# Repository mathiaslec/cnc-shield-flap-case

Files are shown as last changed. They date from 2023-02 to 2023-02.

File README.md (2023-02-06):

# Read the documentation here : https://mathiaslec.github.io/cnc-shield-flap-case/
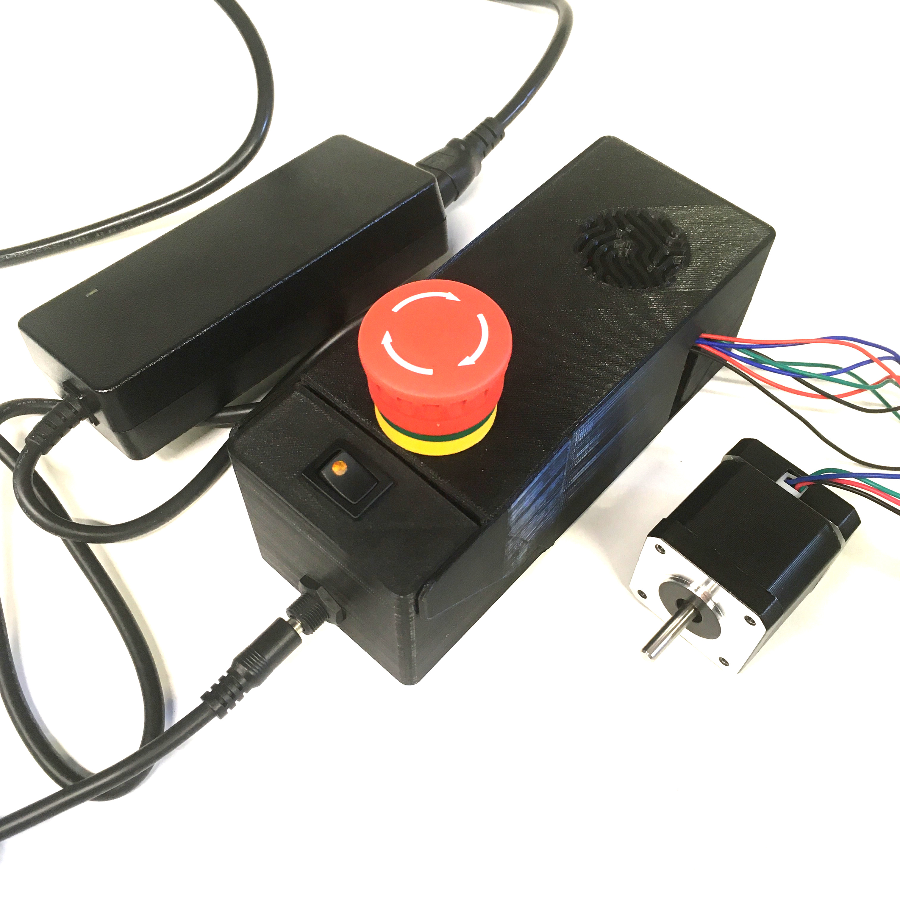
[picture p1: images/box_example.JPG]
  
# This project is documented with GitBuilding

## What is GitBuilding

GitBuilding is an OpenSource project for documenting hardware projects with minimal
effort, so you can stop writing and GitBuilding. GitBuilding is a python program that
works on Windows, Linux, and MacOS. More information on the GitBuilding project, or how
to install GitBuilding please see the [GitBuilding website](http://gitbuilding.io)

## How do I edit the documentation?

To edit the documentation you do not need to install anything, but you will need to
install something to build the final version of the documentation (such as a website).
The documentation files can be opened in a plain text editor such as Windows Notepad,
Notepad++, gedit, VS Code, etc. GitBuilding also comes with a browser-based editor that
displays has a live display of the final HTML documentation.

If you have ever used [markdown](https://www.markdownguide.org/basic-syntax/) you will
notice that the files you are editing are markdown files. GitBuilding uses an extended
markdown syntax (that we call BuildUp). This allows you to keep track of parts in the
documentation. More detail on the documentation is available on the
[GitBuilding website](https://gitbuilding.io/syntax/). There is also additional
[syntax for configuration](https://gitbuilding.io/syntax/buildconfsyntax), and for
[part libraries](https://gitbuilding.io/syntax/builduplibrary/).

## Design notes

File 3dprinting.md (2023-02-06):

# 3D printing

{{BOM}}

The CAD parts for the flap case were created using FreeCAD and are available on the [GitHub repository linked](freecad/cad/psu_xs_V5.FCStd).

The case is composed of three parts: the base, a small lid, and the main lid. The components are made with [PLA](parts.yaml#pla){qty:150g} material using a [FDM 3D printer](tools.yaml#3dprinter){qty:1, cat:tool}.

## Slicing {pagestep}
  
Download the stl files and upload them into your slice : 




We use Cura or Kiri:moto as slicer, with the following paremeters :  

* Layer height : 0.2 mm;
* Infill : 20 %;
* Supports everywhere;
* Wall thickness : 1.2 mm.

This is what the parts look like in the slicer :  
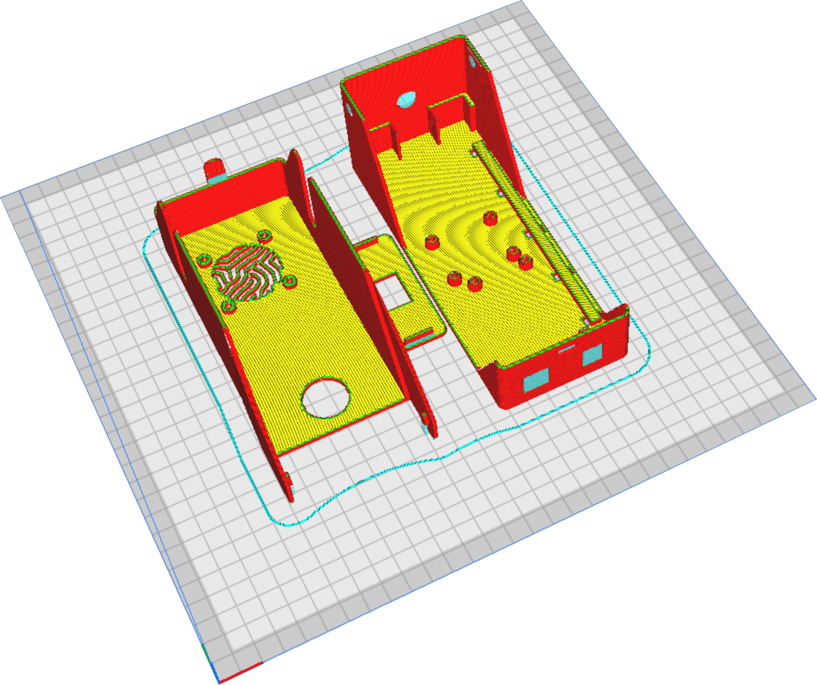
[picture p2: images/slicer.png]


## Post-printing {pagestep}
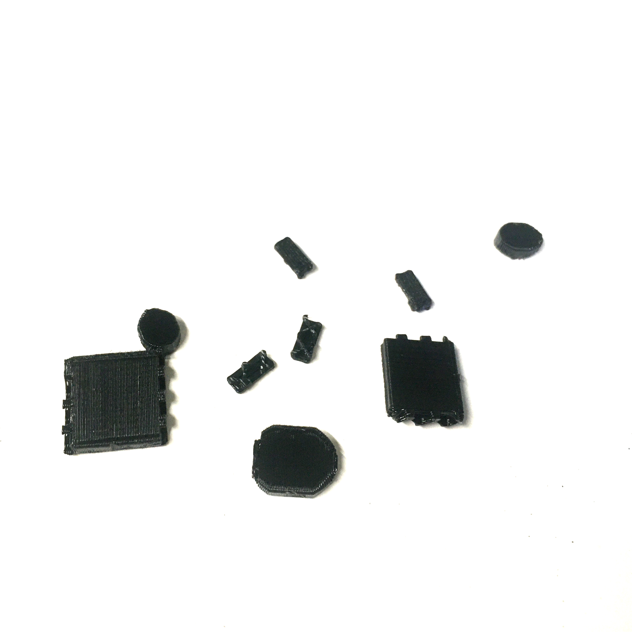
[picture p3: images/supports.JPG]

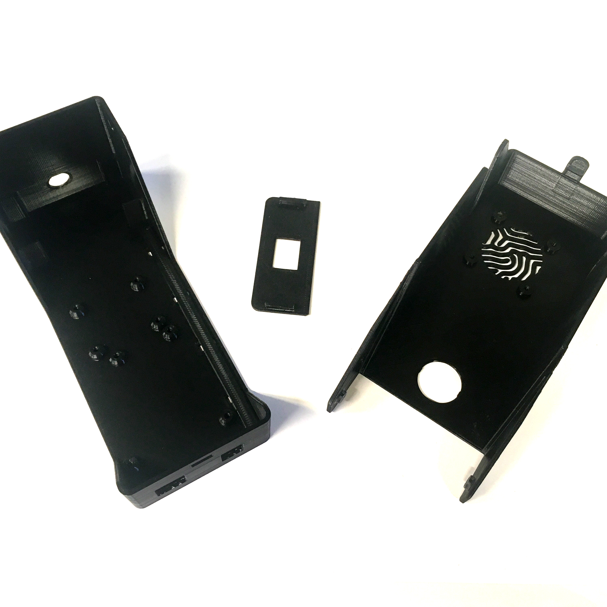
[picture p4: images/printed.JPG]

Once printed, carefully remove all supports.

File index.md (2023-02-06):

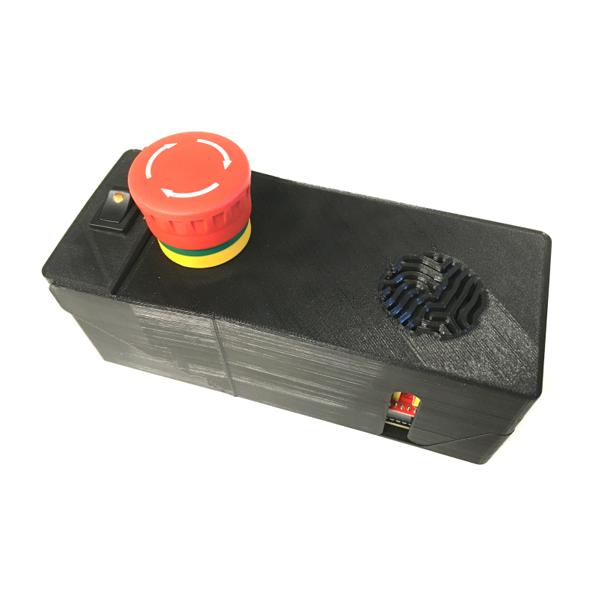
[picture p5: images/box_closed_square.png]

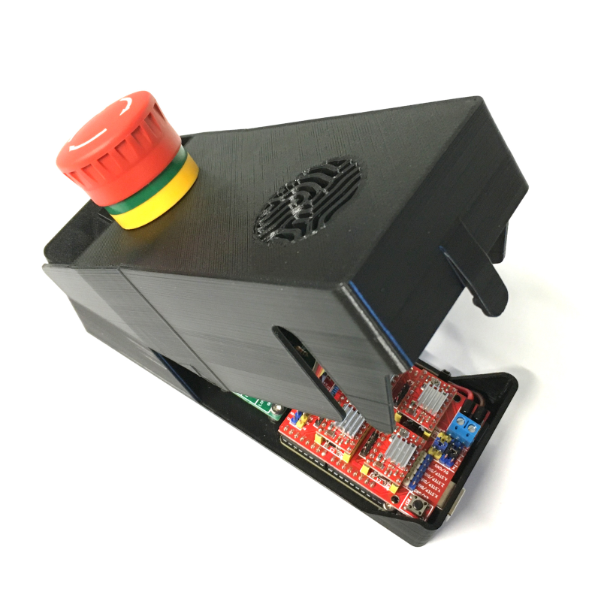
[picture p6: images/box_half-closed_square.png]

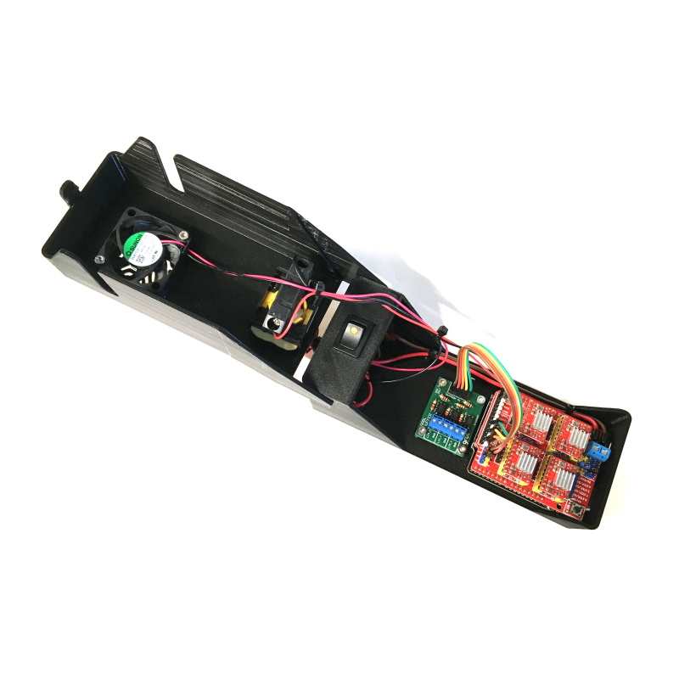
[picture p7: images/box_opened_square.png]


# CNC shield flap case

## Introduction

This is a tutorial on how to make a flap case for a CNC shield compatible with an Arduino Uno board.
Advantages of this flap case for a CNC shield include:

* A switch button with an LED to indicate the power status of the CNC shield and allow for easy ON/OFF control.
* A kill switch for emergency situations with the stepper motors.
* Easy access to the CNC shield for plugging and unplugging of stepper motors and limit switches, thanks to the flap design.

## Content

Here is the [bill of materials]{BOM} page.  
And here are the main steps to follow:

* [.](3dprinting.md){step}
* [.](assembling.md){step}
* [.](testing.md){step}
* [.](more_info.md){step}

## A few explanations about the design
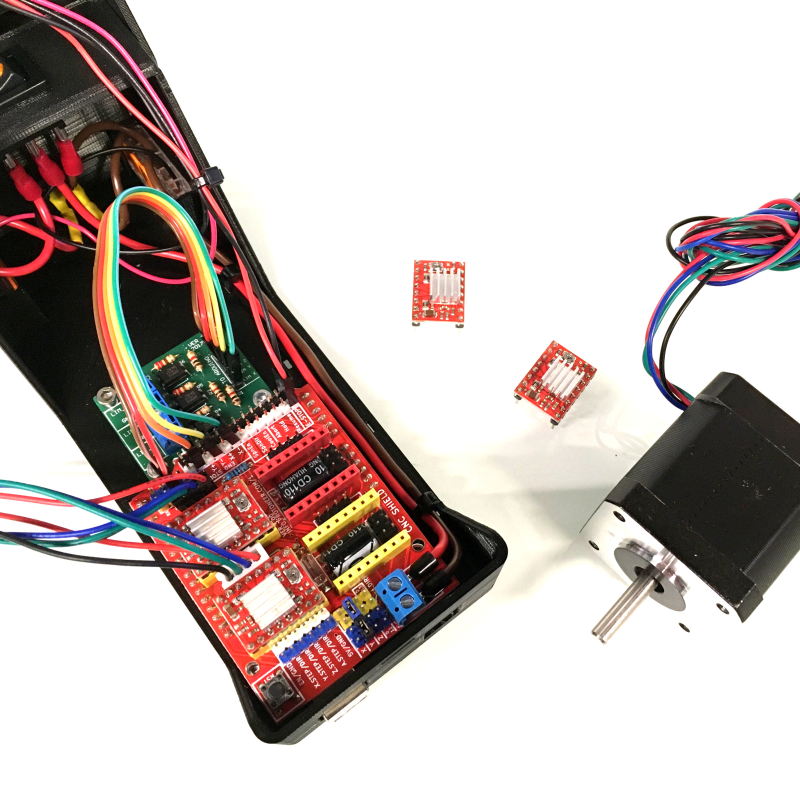
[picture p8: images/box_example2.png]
  
  
As shown in the images, the flap case is designed for easy plugging and unplugging of the stepper motors. The switch button with an LED helps to quickly and safely control the power status of the CNC shield.

Additionally, the flap case offers practicality and a touch of personal flair for those using CNC shields with multiple devices in various locations.

The fan grill on the flap case is a [Turing pattern](https://en.wikipedia.org/wiki/Turing_pattern), reference to the Turing Center for Living Systems, inspired by Alan Turing's work.

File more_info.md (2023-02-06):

# More information
## About the components
The power supply used is 12V 6.67A (80W), which should be enough for driving 4 stepper motors. All components are therefore chosen to carry at least 12V 6.67A (except for the fan which draws 95mA): wires, connectors, etc...

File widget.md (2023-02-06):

---
PartData:
    Specs:
        Type: Unknown
        Quality: Fantastic
    Suppliers:
        Widget Shop:
            PartNo: Widget1
            Link: https://dictionary.cambridge.org/dictionary/english/widget
---

# Widget

This is an example page for a part that needs more information than can be provided
in a part library. You can also add links and images into this page.



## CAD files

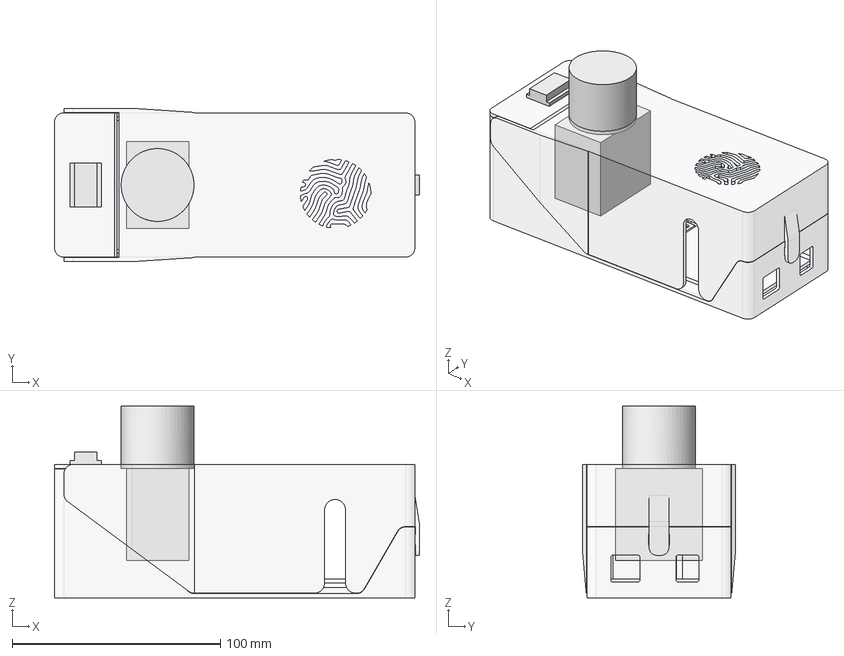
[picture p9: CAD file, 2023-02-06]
freecad/cad/psu_xs_V5.FCStd
175.3 x 73.7 x 92.0 mm
base
small_lid
lid
arduino_board
pcb
estop
switch

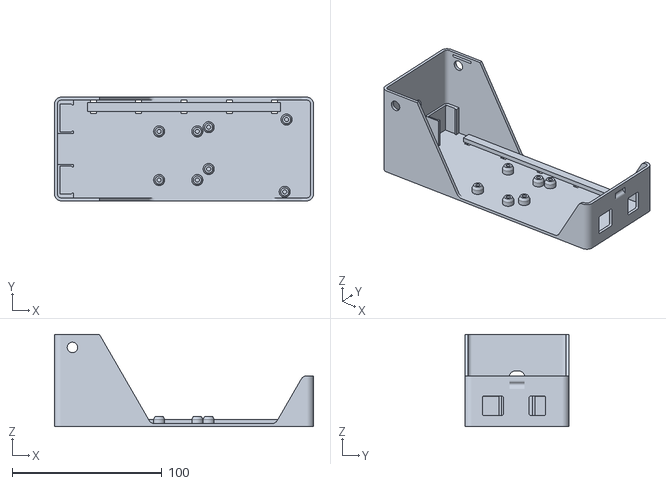
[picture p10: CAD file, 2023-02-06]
freecad/stl/base.stl
173.1 x 69.3 x 61.8

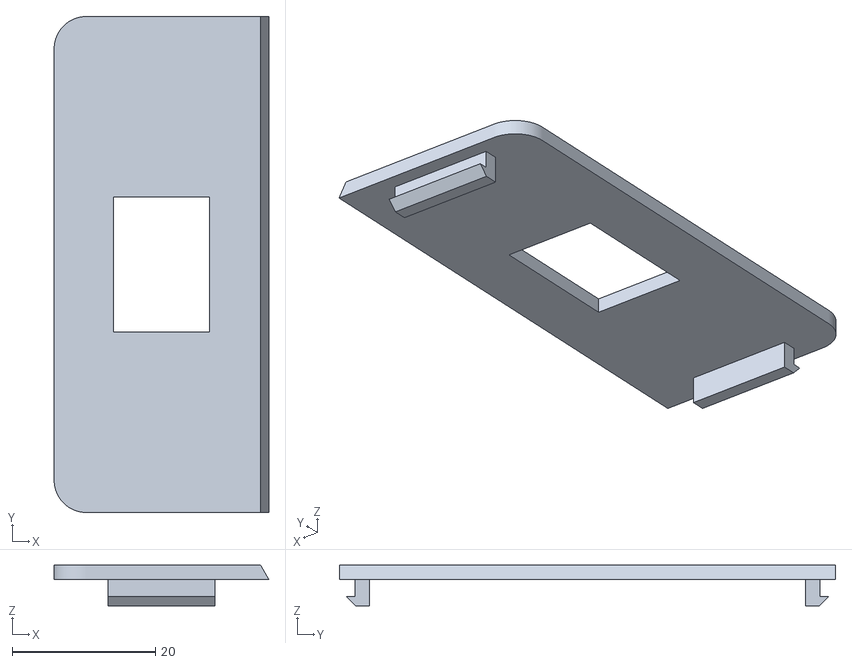
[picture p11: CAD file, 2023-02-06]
freecad/stl/small_lid.stl
30.0 x 69.3 x 5.70

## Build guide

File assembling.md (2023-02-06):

# Assembling

{{BOM}}

## Wiring {pagestep}
Before assembly, you need to prepare a few wires. You will need wire strippers and crimpers to complete this step.
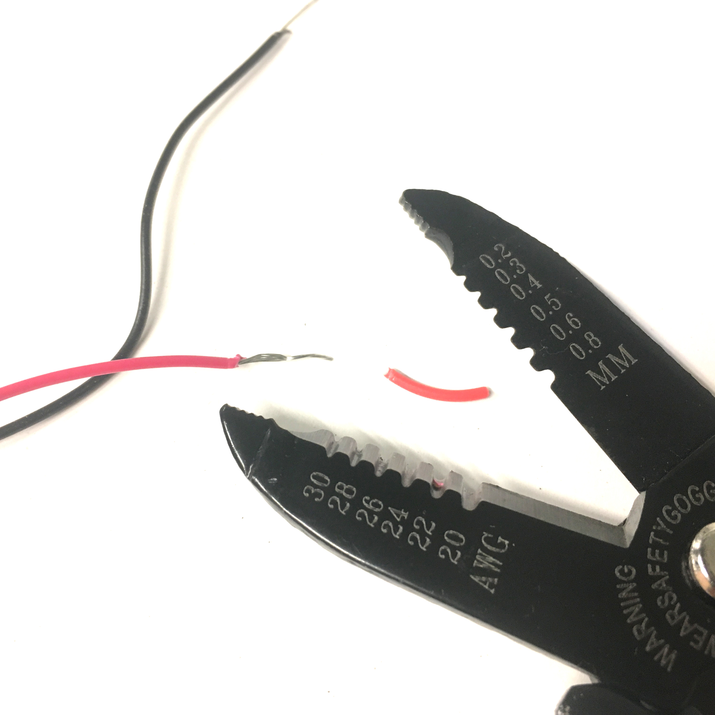
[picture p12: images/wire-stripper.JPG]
  
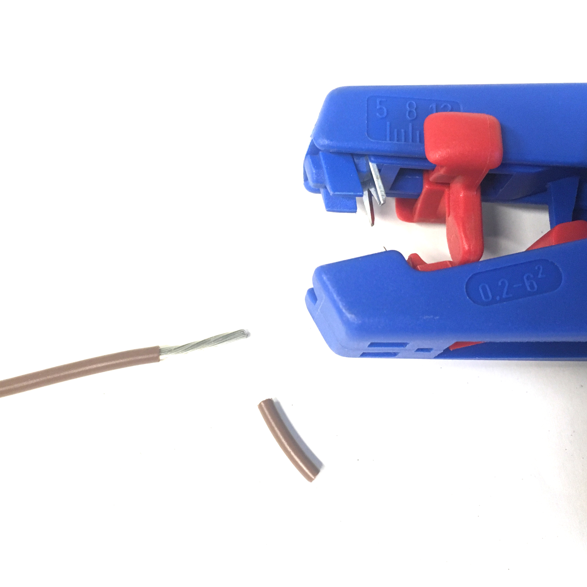
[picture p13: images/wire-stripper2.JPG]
  
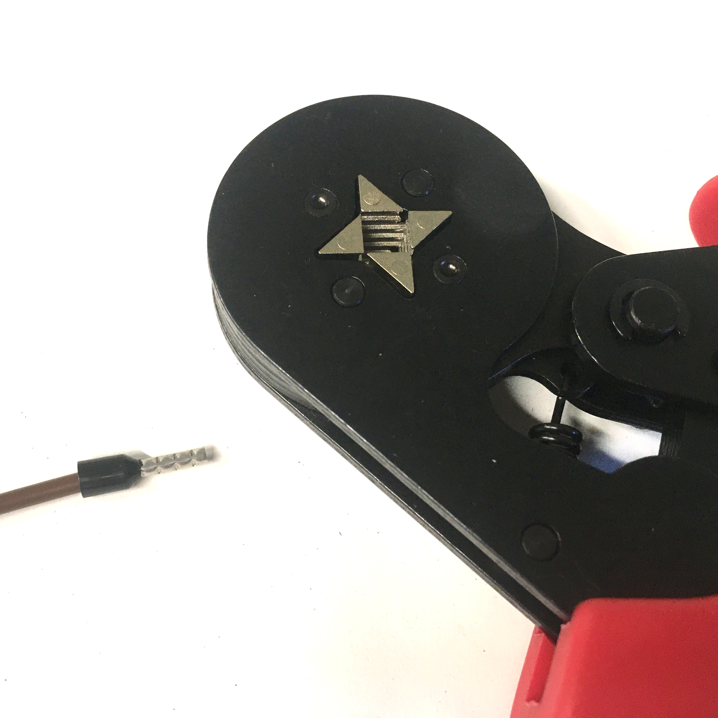
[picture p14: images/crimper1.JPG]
  
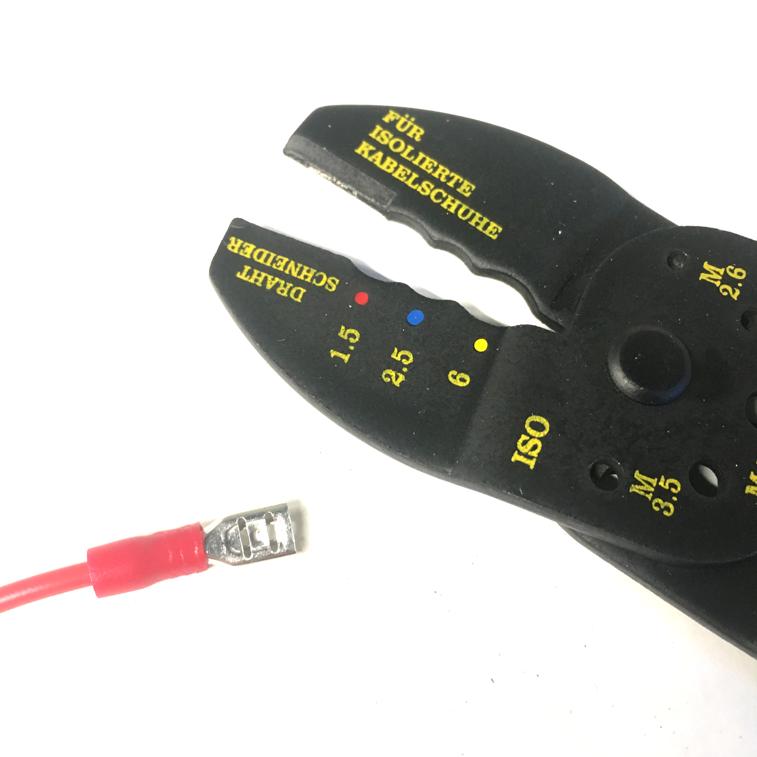
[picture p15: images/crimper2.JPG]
  
 
>i **Note about stripped wires**
>i
>i The length of the stripped wire will depend on the component it is connected to. Make sure to refer to the instructions for each component if you are using different brands. The following reference lengths are provided:  
>i - 11 mm for Wagos  
>i - 8 mm for ferrules  
>i - 5 mm for blade receptacle connectors  
>i These lengths are only guidelines and may vary based on the specific components and wiring requirements, so be sure to consult the instructions for each component before stripping the wires.

### Jumper wires
If you are using the [noise filtering PCB](parts.yaml#NoiseFilteringPCB){qty:1}, you may need up to 5 [jumper wires](parts.yaml#JumperWires){qty:5} to connect the CNC shield to the PCB.  
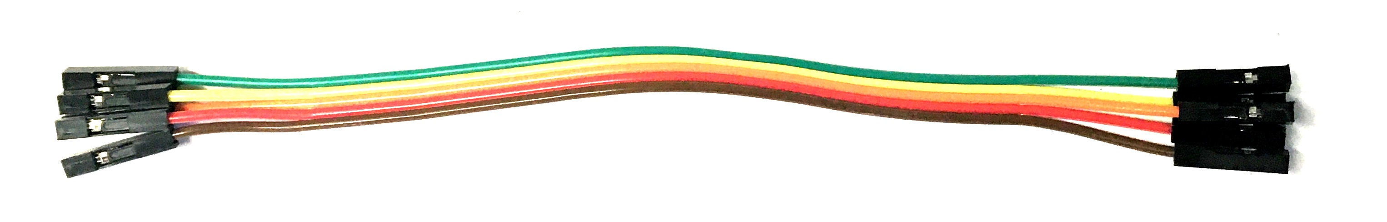
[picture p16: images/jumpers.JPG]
  

### Pre-fab braid
You need 1 [pre-fab braid](parts.yaml#PrefabBraid){qty:1} (to connect to the emergency button to the CNC shield). Just cut the excess of wires to get 20 cm, then strip about 1 cm on each wire with (for example with a [wire stripper](tools.yaml#WireStripper){qty:1, cat:tool}). Attach the stripped wires to the [kill switch](parts.yaml#KillSwitch){qty:1}. 
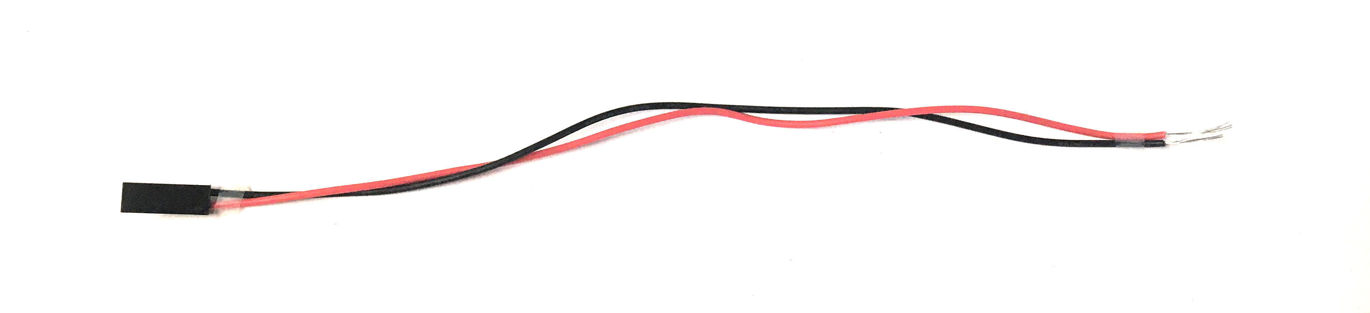
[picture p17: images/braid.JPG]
  
### Connections to power supply
A few wires and components are needed : 

* 8 cm of a [16awg/1.5mm² red wire](parts.yaml#16awgRedWire){qty:8cm}. Strip about 5 mm on one side with the [wire stripper](tools.yaml#WireStripper), and solder this wire (with a [soldering iron](tools.yaml#SolderingIron){qty:1,cat:tool} and [soldering wire](parts.yaml#SolderingWire)) to the **central pin** of the [DC connector socket](parts.yaml#DCconnector){qty:1}. Make sure to add about 15 mm long [heat-shrink tube](parts.yaml#Heatshrink){qty:15mm} of suitable diameter. Strip the other end of the wire of about 11 mm.
* 8 cm of a [16awg/1.5mm² black wire](parts.yaml#16awgBlackWire){qty:8cm}. Strip about 5 mm on one side with the [wire stripper](tools.yaml#WireStripper), and solder this wire (with a [soldering iron](tools.yaml#SolderingIron){qty:1,cat:tool} and [soldering wire](parts.yaml#SolderingWire)) to the **external pin** of the [DC connector socket](parts.yaml#DCconnector). Make sure to add about 15 mm long [heat-shrink tube](parts.yaml#Heatshrink){qty:15mm} of suitable diameter. Strip the other end of the wire of about 11 mm.  
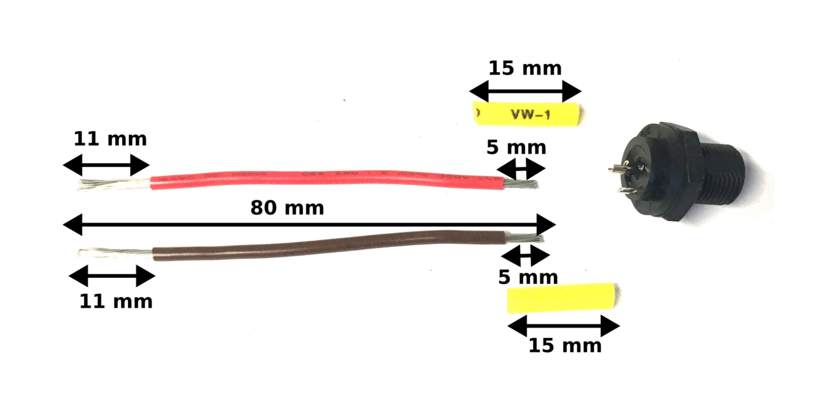
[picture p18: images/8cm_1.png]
   
* Another 8 cm long [16awg/1.5mm² red wire]{qty:8cm}. Strip one side of this wire on about 11 mm, and strip the other end on about 5 mm and add a [blade receptacle connector](parts.yaml#BladeReceptacleConnector){qty:1}. Crimp the blade connector with a [crimping pliers](tools.yaml#CrimpingPliers){qty:1,cat:tool}.
* Another 8 cm long [16awg/1.5mm² black wire](parts.yaml#16awgBlackWire){qty:8cm}. Strip one side of this wire on about 11 mm, and strip the other end on about 5 mm and add a [blade receptacle connector](parts.yaml#BladeReceptacleConnector){qty:1}. Crimp the blade connector with a [crimping pliers](tools.yaml#CrimpingPliers){qty:1,cat:tool}.
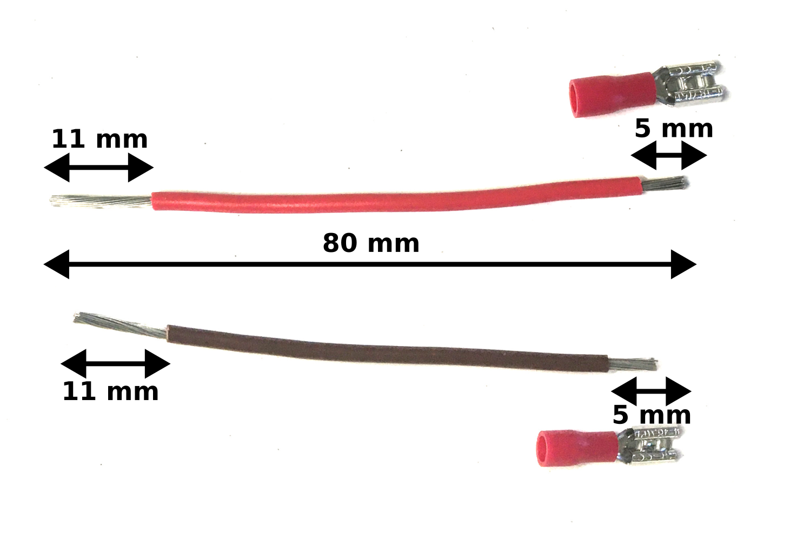
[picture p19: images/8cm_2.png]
   
* 20 cm of a [16awg/1.5mm² black wire](parts.yaml#16awgBlackWire){qty:20cm}. Strip one side of this wire on about 11 mm, then strip the other end on about 5 mm and add a [blade receptacle connector](parts.yaml#BladeReceptacleConnector){qty:1}.
* 20 cm of a [16awg/1.5mm² red wire](parts.yaml#16awgRedWire){qty:20cm}. Strip one side of this wire on about 8 mm, and add a [ferrule](parts.yaml#Ferrule){qty:1}, then strip the other end on about 5 mm and add a [blade receptacle connector](parts.yaml#BladeReceptacleConnector){qty:1}.
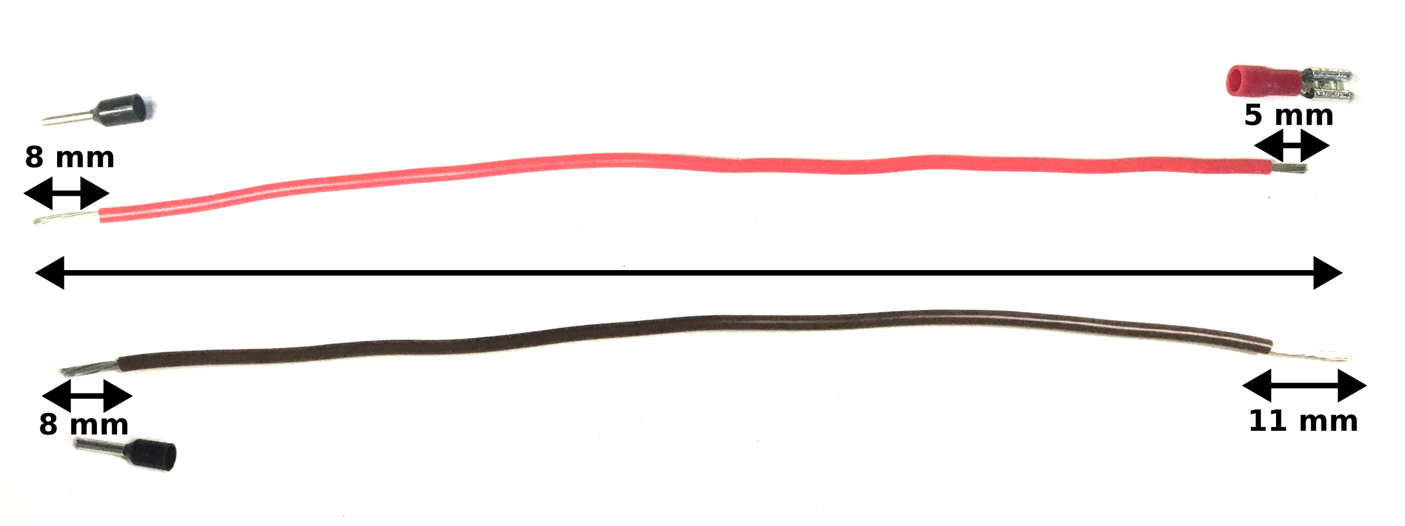
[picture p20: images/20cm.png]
   

Here are all the 16awg/1.5mm² wires:  
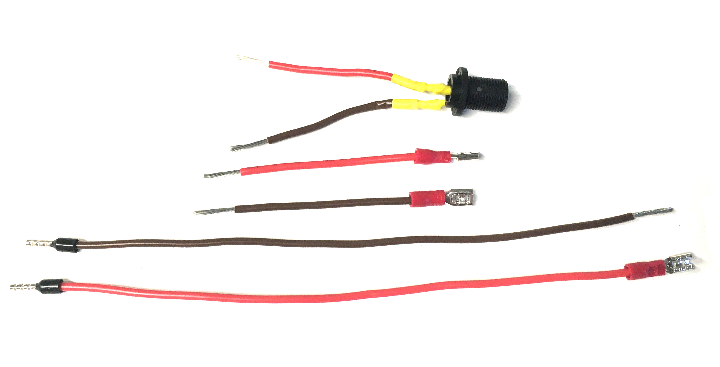
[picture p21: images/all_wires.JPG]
   

### Fan wires
Make sure the [fan](parts.yaml#Fan){qty:1} wires are about 30 cm long, then strip about 11 mm on each end.
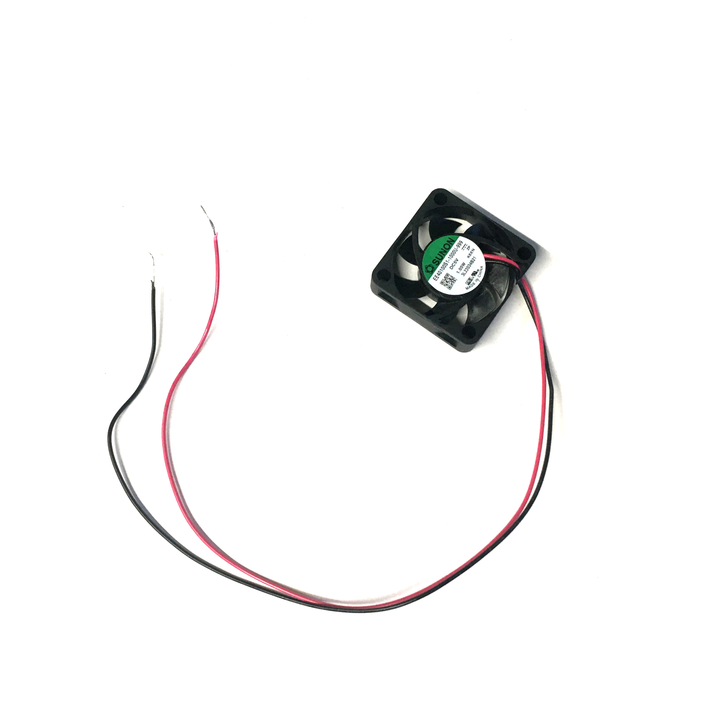
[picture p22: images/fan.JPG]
   

## First components to attach {pagestep}
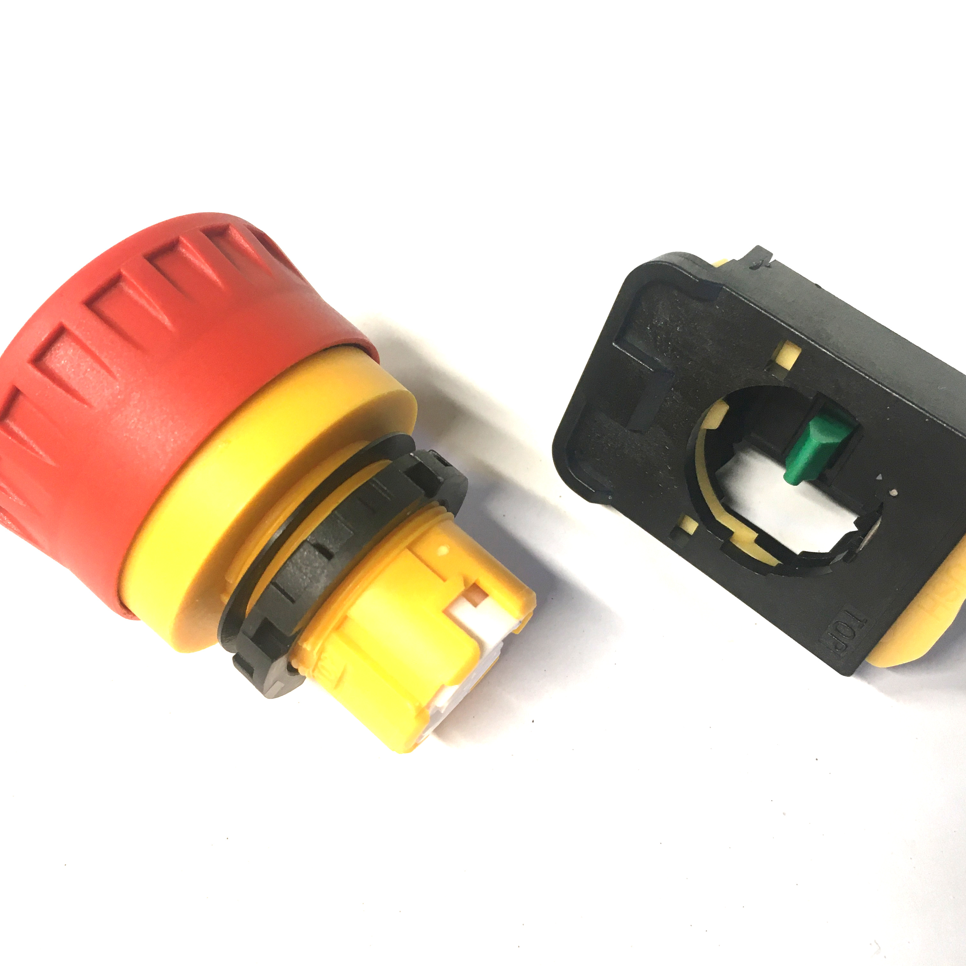
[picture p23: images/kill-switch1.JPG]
   
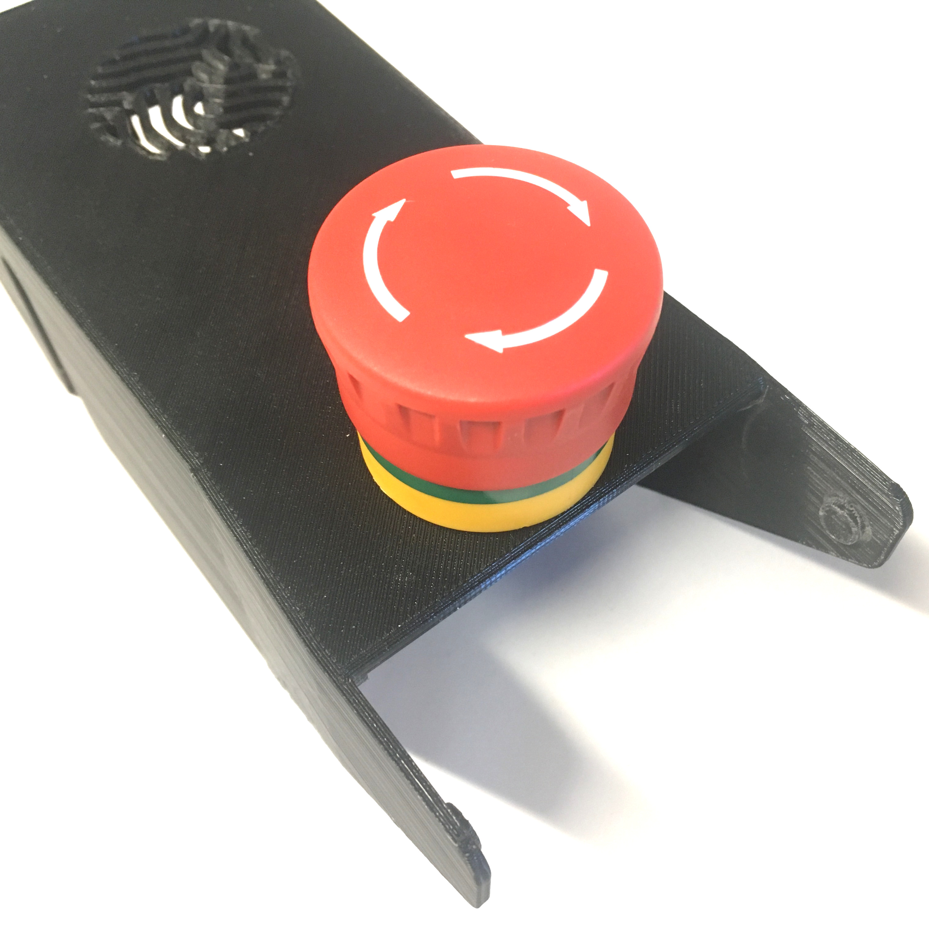
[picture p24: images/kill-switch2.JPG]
   
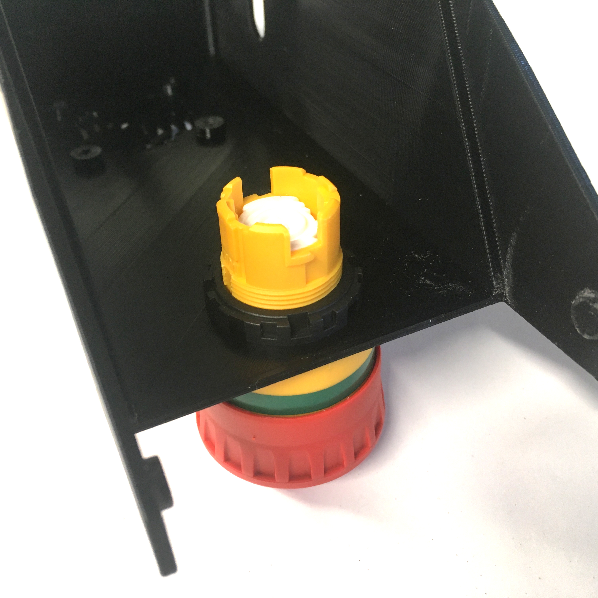
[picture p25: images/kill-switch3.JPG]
   
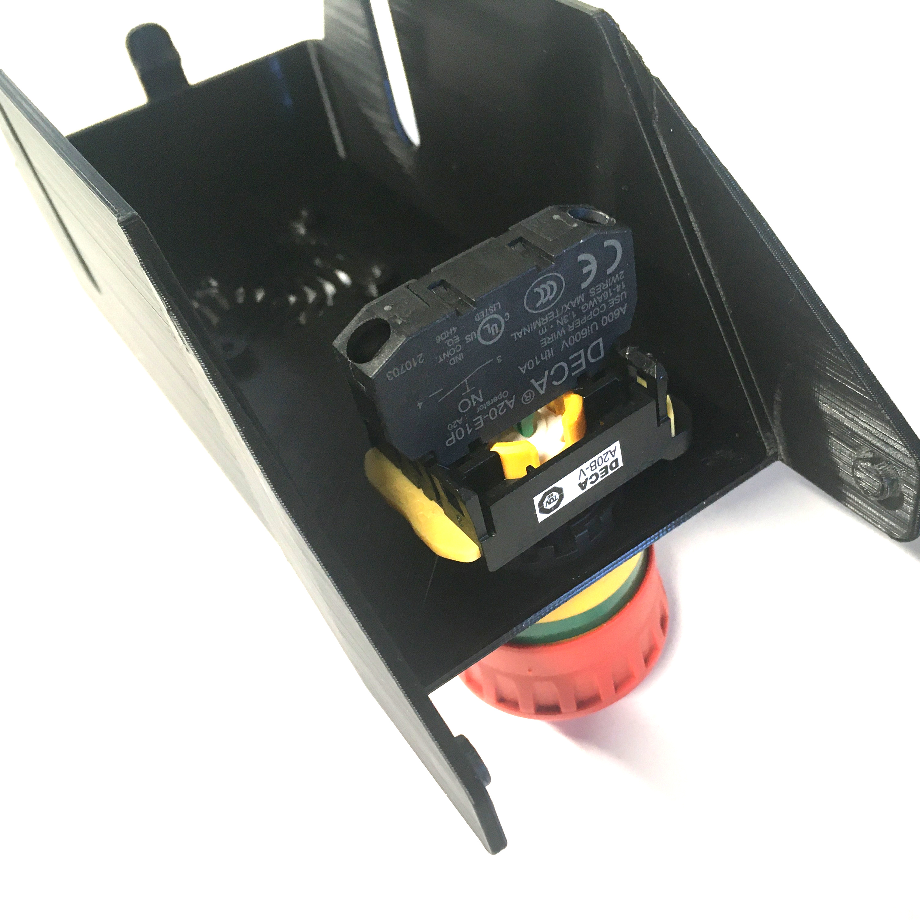
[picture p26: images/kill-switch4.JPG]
   
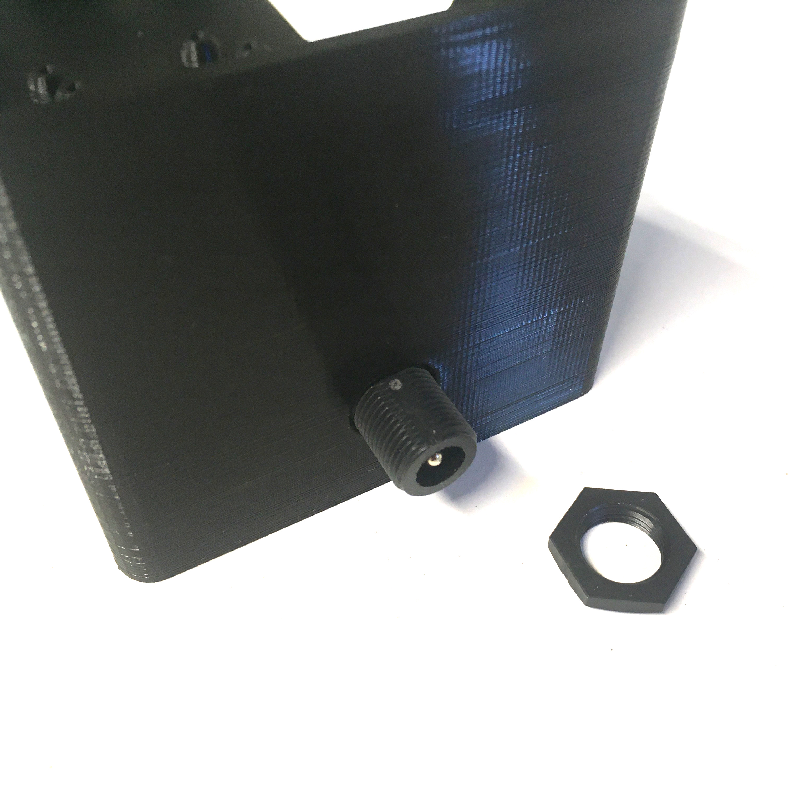
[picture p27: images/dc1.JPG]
   
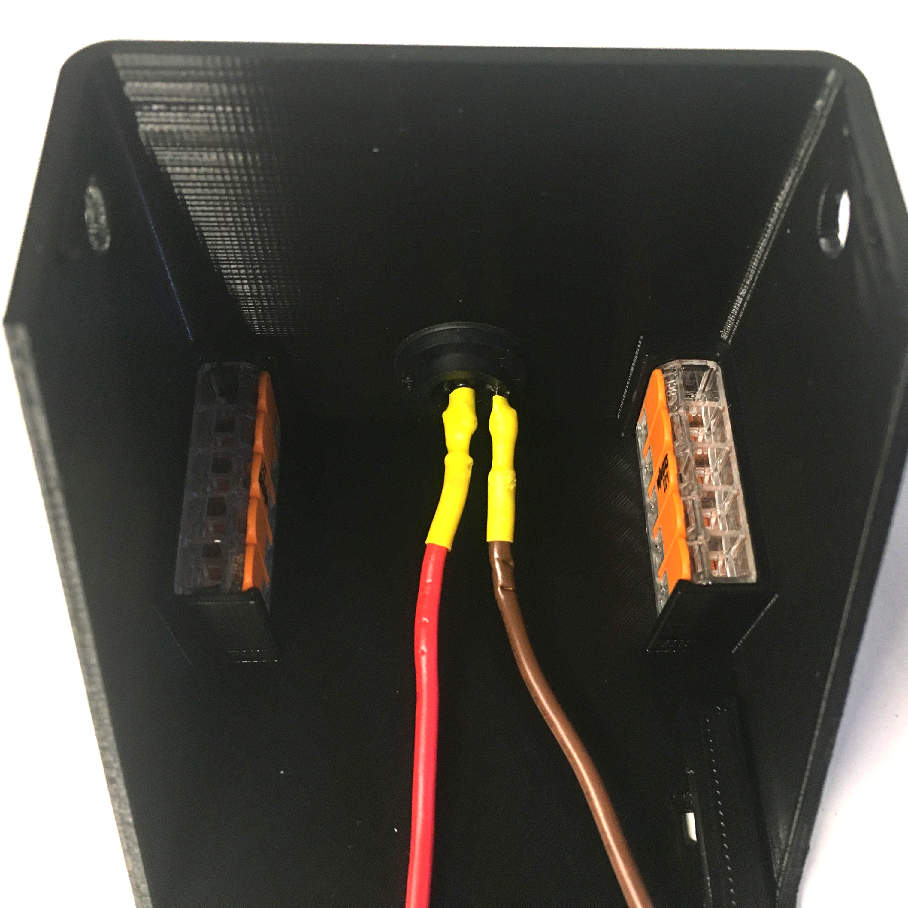
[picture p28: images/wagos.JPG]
 
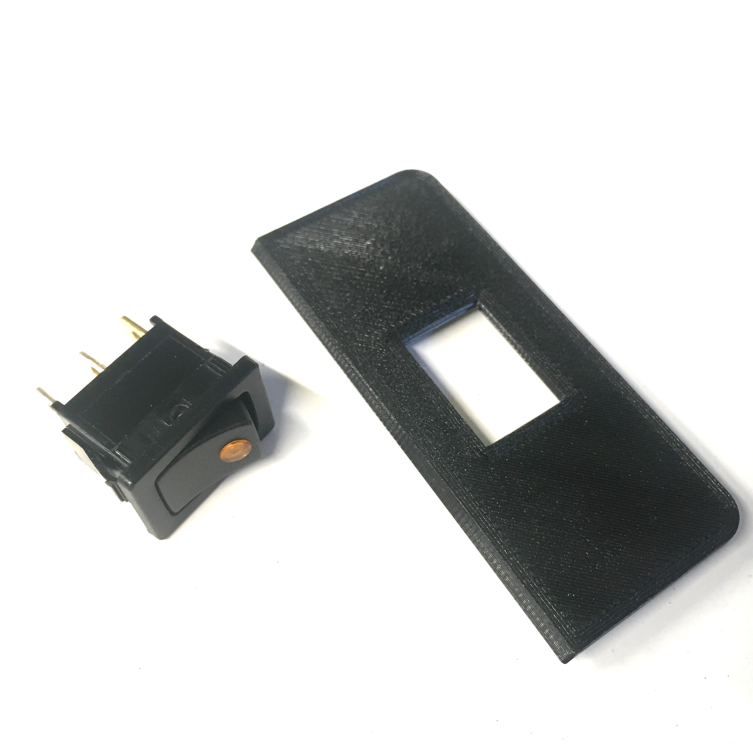
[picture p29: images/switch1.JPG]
 
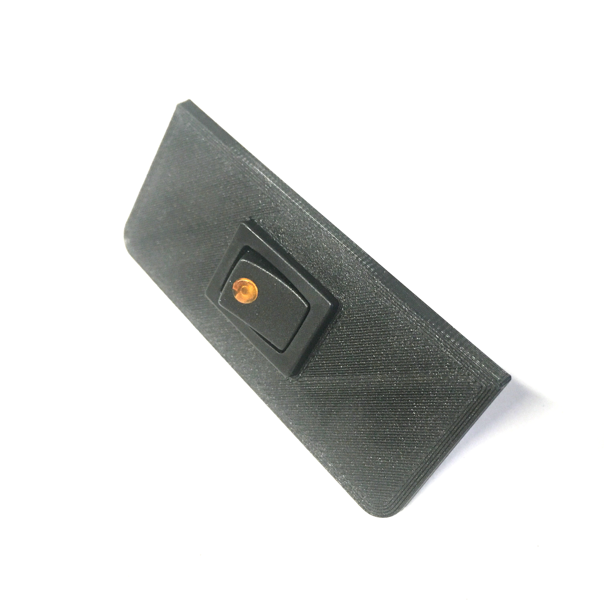
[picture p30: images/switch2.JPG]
 
The following components are easy to install into the case:

* Detach the 2 parts of the [kill switch](parts.yaml#KillSwitch), place the button on the lid, attach it with its plastic nut, then clip the last part to fully assemble it.  
* Attach the DC connector into the case.
* Clip both [wagos](parts.yaml#Wagos){qty:2} into the case.
* Snap-in the [toggle switch](parts.yaml#ToggleSwitch){qty:1} to the small lid. 

## Components attached with screws {pagestep}
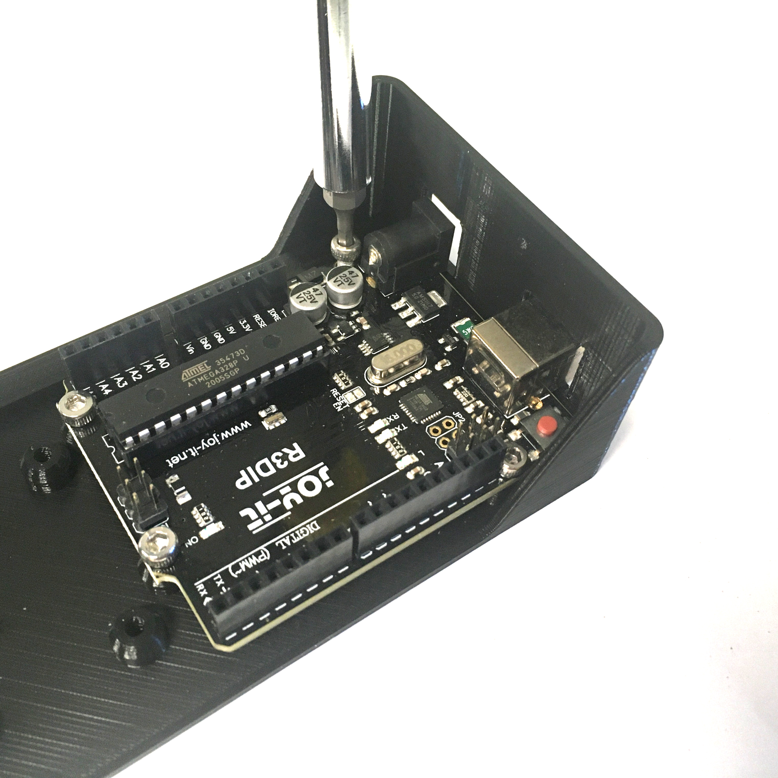
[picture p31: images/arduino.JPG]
 
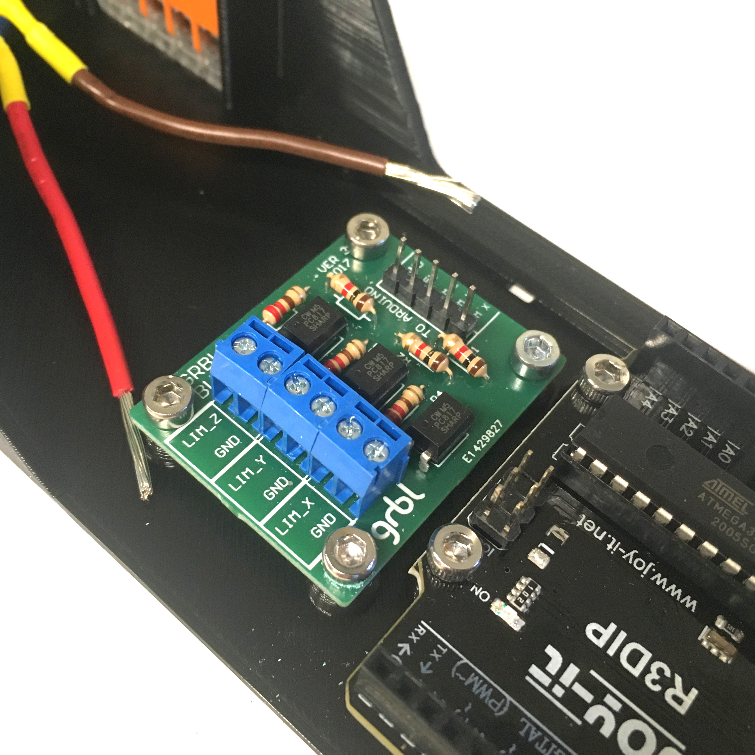
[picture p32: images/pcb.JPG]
 
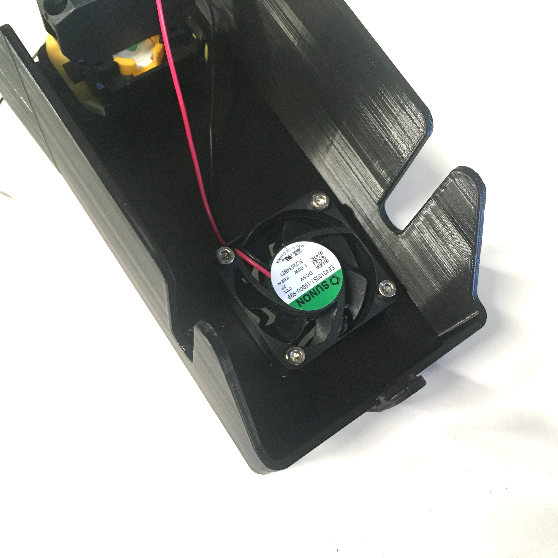
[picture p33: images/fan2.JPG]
 
A few components need screws to attach them to the box:

* The [Arduino Uno board](parts.yaml#Arduino){qty:1} needs 4 [M3x6mm screws](parts.yaml#M3x6mm){qty:4}. 
* The [noise filtering PCB](parts.yaml#NoiseFilteringPCB) needs 4 [M3x6mm screws](parts.yaml#M3x6mm){qty:4};
* The [fan](parts.yaml#Fan) needs 4 [M3x12mm screws](parts.yaml#M3x12mm){qty:4}.

Note: Use an [Allen wrench](tools.yaml#AllenWrench){qty:1,cat:tool} to attach the components securely.

## Final assembling {pagestep}
### Wiring
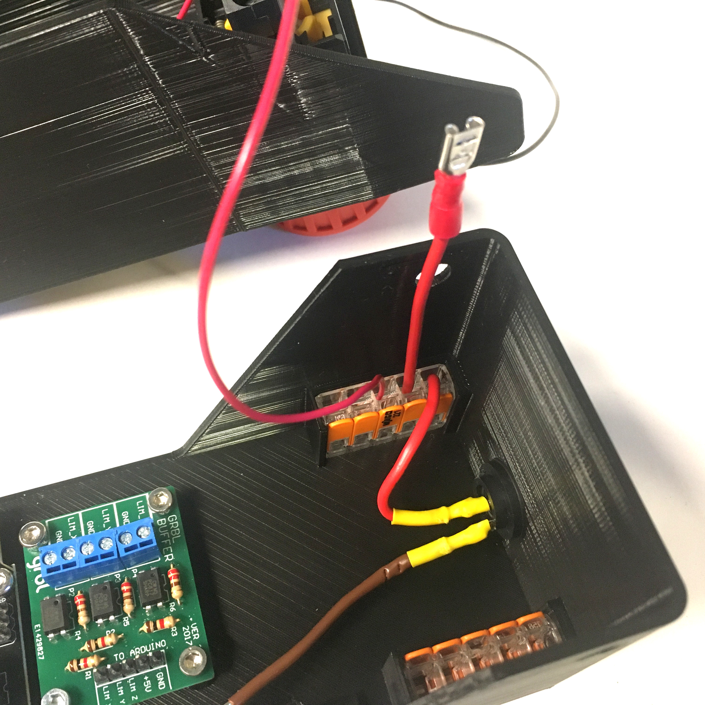
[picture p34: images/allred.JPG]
 
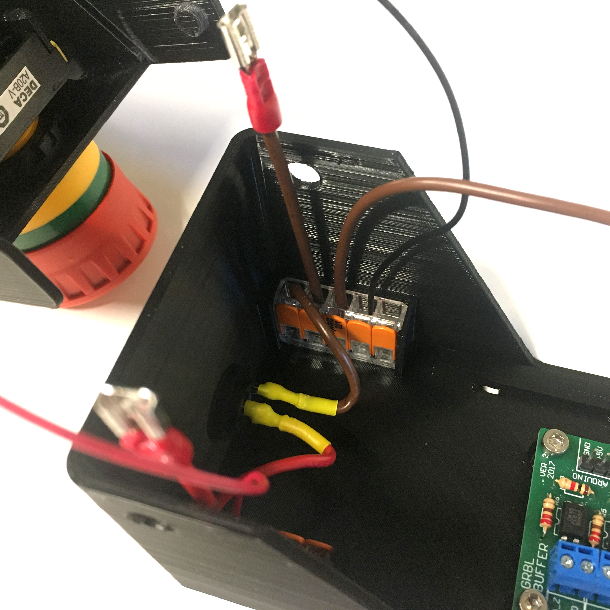
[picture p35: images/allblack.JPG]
 
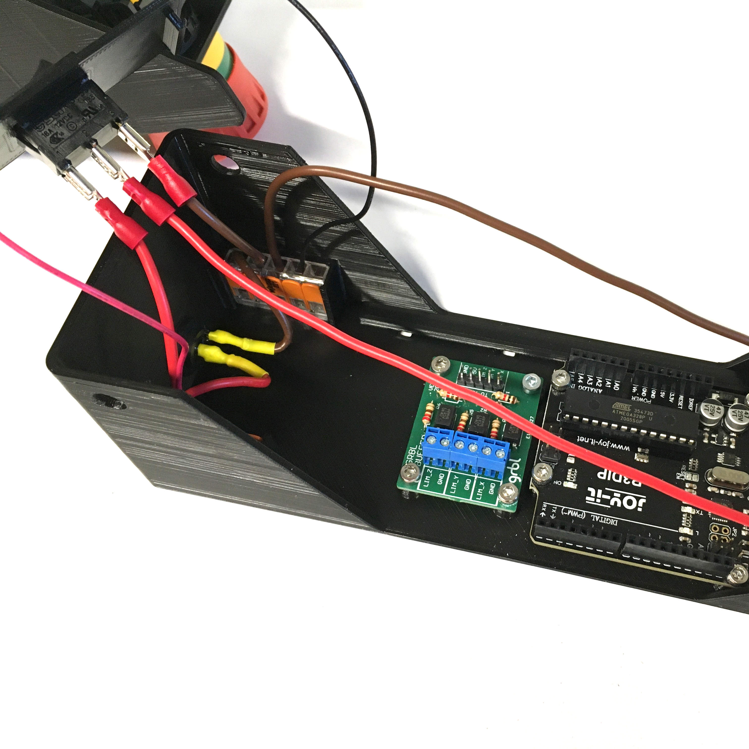
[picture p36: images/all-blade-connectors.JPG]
 
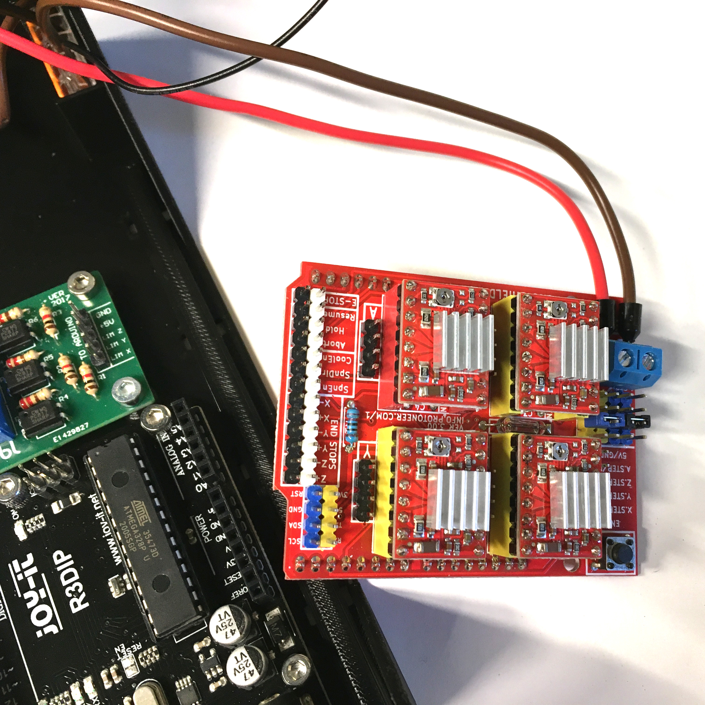
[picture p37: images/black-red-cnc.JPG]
 
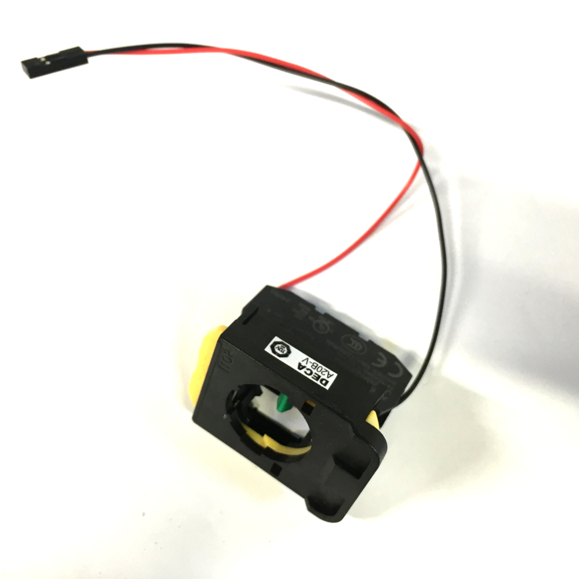
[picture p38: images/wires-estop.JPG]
 
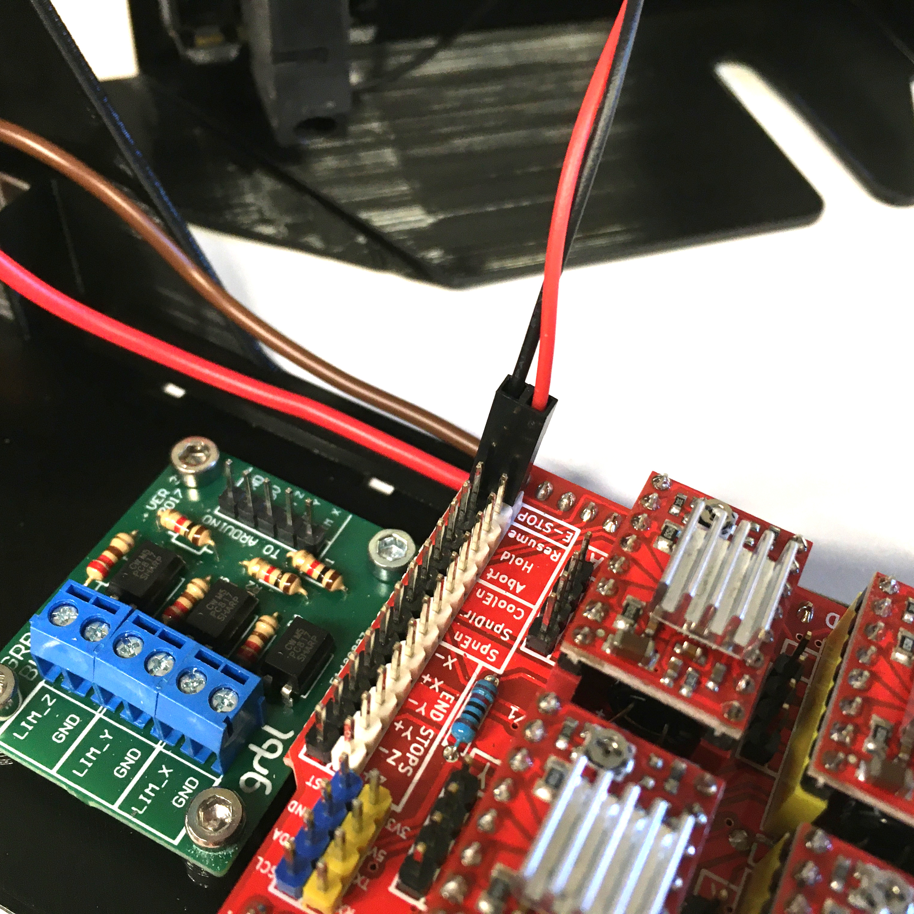
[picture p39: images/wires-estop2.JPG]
 
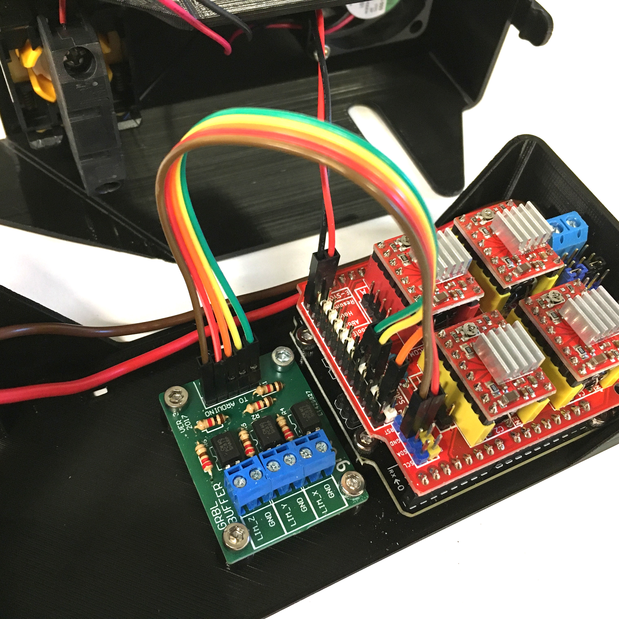
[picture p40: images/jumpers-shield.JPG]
 
The last steps for the wiring are the following:

* Insert all red stripped wires into 1 [wago](parts.yaml#Wagos).
* Insert all black stripped wires into the other [wago](parts.yaml#Wagos).
* Attach the blade receptacle connector from the 8 cm black wire to the colored pin of the toggle switch (the one below the orange light). *If you bought another toggle switch, make sure to read the datasheet to check were the GND should be plugged*.
* Attach the blade receptacle connector from the 8 cm red wire to the opposite pin of the toggle switch.
* Attach the blade receptacle connector from the 20 cm long red wire to the centered pin of the toggle switch.
* Finally, insert the 20 cm long black and red wires with the ferrules into the "-" and "+" terminal block of the CNC shield, then tighten the screws with a [small flat screwdriver](tools.yaml#FlatScrewdriver){qty:1,cat:tool}. You can then plug the [CNC shield](parts.yaml#CNCShield){qty:1}.

There are now a few wires to plug:  

* Attach the [pre-fab braid](parts.yaml#PrefabBraid) to the kill switch, and to the "E-STOP" pins on the CNC shield.
* If you have a noise filtering PCB, plug it with the 5 jumper wires to the CNC shield.

### Assemble the case
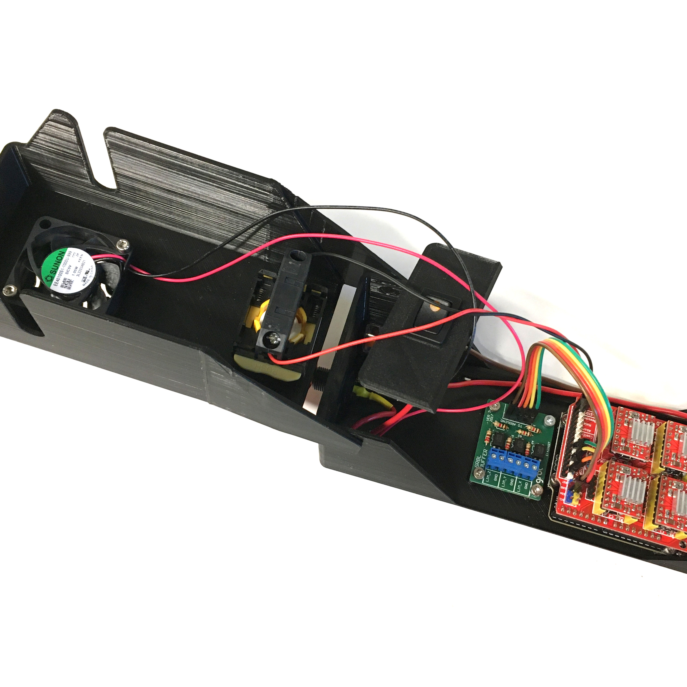
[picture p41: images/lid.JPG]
 
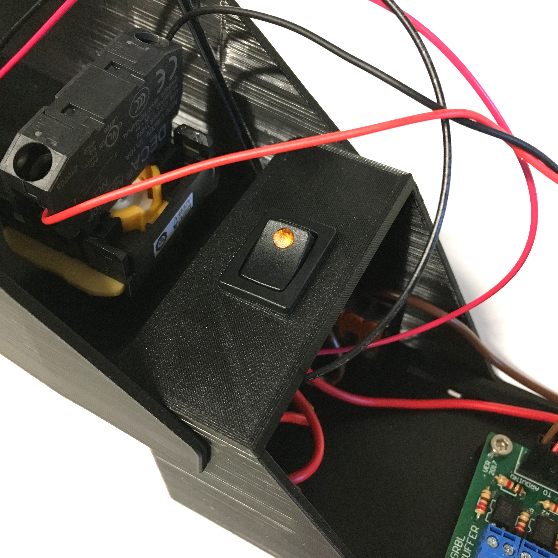
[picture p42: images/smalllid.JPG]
 
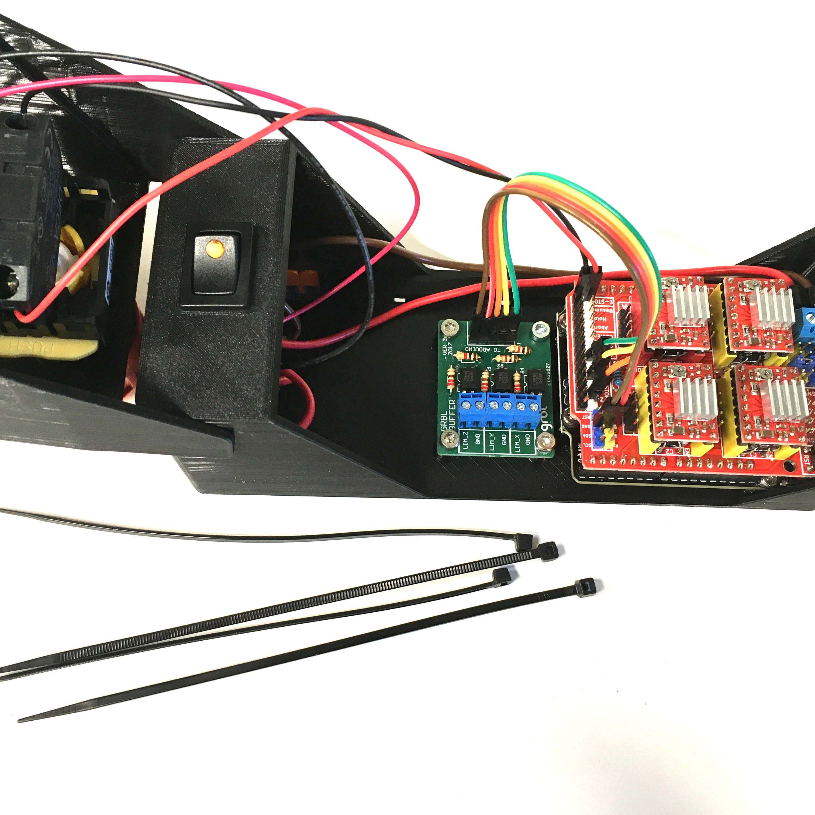
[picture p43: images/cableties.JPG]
 
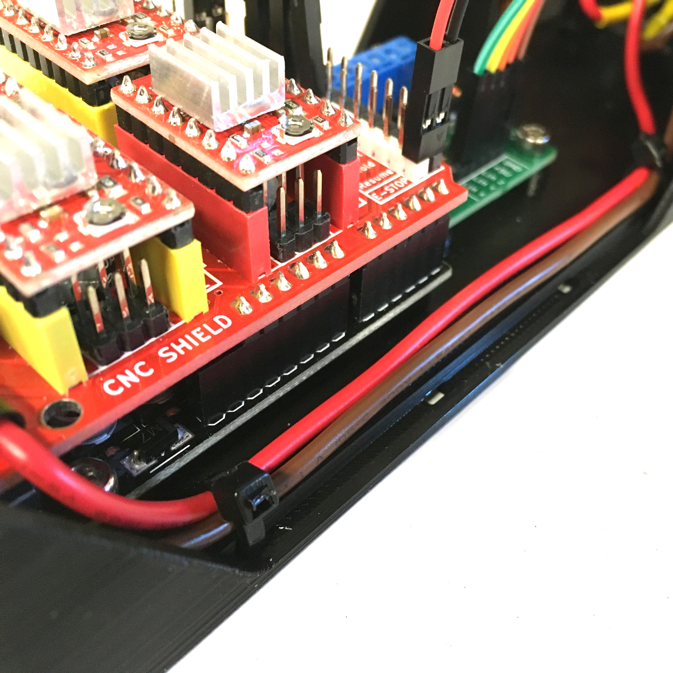
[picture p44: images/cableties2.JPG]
 
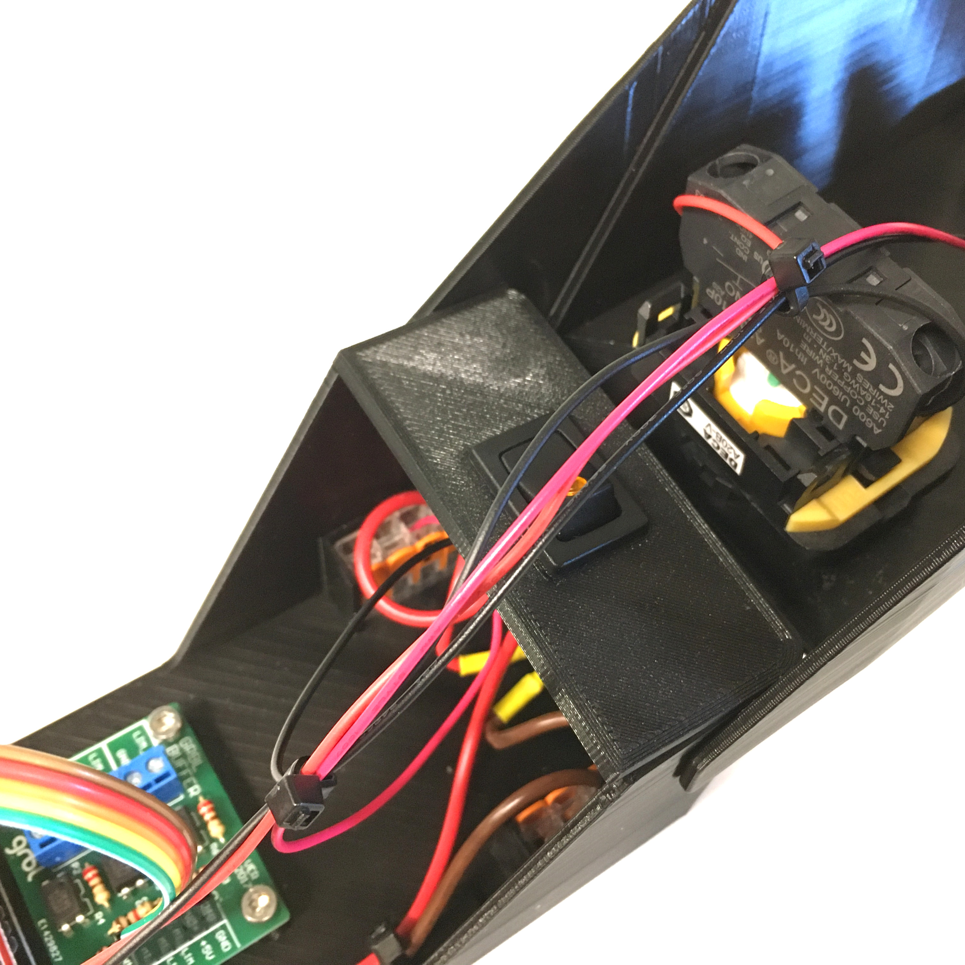
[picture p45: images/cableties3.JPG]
 
Attach the small lid then the lid onto the base.

Now to organize these wires, you can use 2 [cable ties](parts.yaml#CableTies){qty:2} to attach the 20 cm long wires to the case, and 2 other [cable ties](parts.yaml#CableTies){qty:2} to attach the kill switch and fan wires together.

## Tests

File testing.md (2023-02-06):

 # Testing
{{BOM}}

A [12V 80W power supply](parts.yaml#PowerSupply){qty:1} should be enough to power the CNC shield. And a [USB B cable](parts.yaml#USBCable){qty:1} is needed to power the Arduino board.  

You are now ready to use the CNC shield flap case !


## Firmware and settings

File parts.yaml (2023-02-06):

name: 
    Name:
    Suppliers:
        Conrad:
            PartNo:
            Link: 
USBCable: 
    Name: USB B cable
    Suppliers:
        Conrad:
            PartNo: AK-300105-005-S
            Link: https://www.conrad.fr/fr/p/digitus-cable-usb-usb-2-0-usb-a-male-usb-b-male-0-50-m-noir-ak-300105-005-s-678048.html
PowerSupply: 
    Name: 12V 80W power supply
    Suppliers:
        Conrad:
            PartNo: GSM90A12-P1M
            Link: https://www.conrad.fr/fr/p/alimentation-de-table-a-tension-fixe-mean-well-gsm90a12-p1m-n-a-6-67-a-80-w-1-pc-s-1838030.html
CableTies: 
    Name: Cable ties
    Suppliers:
        Conrad:
            PartNo: 1577931
            Link: https://www.conrad.fr/fr/p/tru-components-1577931-serre-cable-120-mm-2-mm-blanc-stabilise-a-la-chaleur-100-pc-s-1577931.html
CNCShield: 
    Name: CNC Shield
    Suppliers:
        Conrad:
            PartNo: ARD-CNC-Kit1
            Link: https://www.conrad.fr/fr/p/joy-it-ard-cnc-kit1-convient-pour-cartes-arduino-arduino-uno-1-pc-s-1646889.html
M3x12mm: 
    Name: M3 x 12 mm screws
    Suppliers:
        Conrad:
            PartNo: 888739
            Link: https://www.conrad.fr/fr/p/vis-cylindrique-toolcraft-888739-1-pc-s-m3-12-mm-tete-cylindrique-6-pans-interieurs-acier-inoxydable-n-a-888739.html
M3x6mm: 
    Name: M3 x 6 mm screws
    Suppliers:
        Conrad:
            PartNo: 888735
            Link: https://www.conrad.fr/fr/p/vis-cylindrique-toolcraft-888735-1-pc-s-m3-6-mm-tete-cylindrique-6-pans-interieurs-acier-inoxydable-n-a-888735.html
Arduino: 
    Name: Arduino Uno board
    Suppliers:
        Conrad:
            PartNo: A000066
            Link: https://www.conrad.fr/fr/p/carte-arduino-uno-rev3-version-dip-atmega328-1275279.html
ToggleSwitch: 
    Name: Toggle Switch
    Suppliers:
        Conrad:
            PartNo: 1587832
            Link: https://www.conrad.fr/fr/p/interrupteur-a-bascule-tru-components-tc-r13-66b2-02-b-b-1587832-12-v-dc-16-a-1-x-off-on-a-accrochage-1-pc-s-1587832.html
Wagos: 
    Name: 5 pins Wagos
    Suppliers:
        Conrad:
            PartNo: 1188438
            Link: https://www.conrad.fr/fr/p/borne-de-raccordement-wago-221-415-1-flexible-0-14-4-mm-rigide-0-2-4-mm-nombre-de-poles-num-5-transparent-orange-1188438.html
Fan: 
    Name: 12V fan
    Suppliers:
        Conrad:
            PartNo: 171007
            Link: https://www.conrad.fr/fr/p/sunon-ee40101s1-1000u-999-ventilateur-axial-12-v-dc-13-93-m-h-l-x-l-x-h-40-x-40-x-10-mm-1969356.html
16awgRedWire: 
    Name: 16AWG/1.5mm² Red Wire
    Suppliers:
        Conrad:
            PartNo: 29133
            Link: https://www.conrad.fr/fr/p/helukabel-29133-fil-de-cablage-h07v-k-1-x-1-50-mm-rouge-marchandise-vendue-au-metre-1524578.html
16awgBlackWire: 
    Name: 16AWG/1.5mm² Black Wire
    Suppliers:
        Conrad:
            PartNo: 29129
            Link: https://www.conrad.fr/fr/p/helukabel-29129-fil-de-cablage-h07v-k-1-x-1-50-mm-noir-marchandise-vendue-au-metre-1524579.html
Heatshrink: 
    Name: Heat-shrink tubes
    Suppliers:
        Conrad:
            PartNo: HAS07
            Link: https://www.conrad.fr/fr/p/toolland-has07-assortiment-de-gaines-thermoretractables-noir-1-set-2574855.html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
Ferrule: 
    Name: Ferrules
    Suppliers:
        Conrad:
            PartNo: 2620348
            Link: https://www.conrad.com/p/quadrios-22c428-ferrule-15-mm-partially-insulated-black-1-set-2620348
BladeReceptacleConnector: 
    Name: Blade Receptacle Connector
    Suppliers:
        Conrad:
            PartNo: 396108S
            Link: https://www.conrad.com/p/vogt-verbindungstechnik-396108s-blade-receptacle-connector-width-48-mm-connector-thickness-08-mm-180-insulated-re-732370
SolderingWire:
    Name: Soldering Wire
DCconnector:
    Name: DC connector socket
    Suppliers:
        Conrad:
            PartNo: 93038c237
            Link: https://www.conrad.fr/fr/p/connecteur-basse-tension-embase-femelle-tru-components-93038c237-interieur-5-5-mm-2-5-mm-1-pc-s-1497959.html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
KillSwitch:
    Name: Kill switch
    Description: >
        You need a NO kill switch to plug on the CNC shield.
    Suppliers:
        Conrad:
            PartNo: 1233788
            Link: https://www.conrad.fr/fr/p/deca-a20b-v4e20r-arret-d-urgence-avec-element-de-contact-240-v-ac-6-a-2-no-t-ip65-1-pc-s-1233788.html
PrefabBraid:
    Name: Pre-fab braid
    Description: >
        This are just two 26AWG/0.13mm² wires attached to the same double femelle dupont connector. We need only 20 cm or wire.
    Specs:
        Length: 20 cm. Cut the excess if needed.
    Suppliers:
        Conrad:
            PartNo: 1570820
            Link: https://www.conrad.fr/fr/p/cordon-fil-a-carte-assemble-tru-components-741213-nbr-total-de-poles-2-pas-2-54-mm-1-pc-s-1570820.html
NoiseFilteringPCB:
    Name: Noise filtering PCB
    Description: >
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
